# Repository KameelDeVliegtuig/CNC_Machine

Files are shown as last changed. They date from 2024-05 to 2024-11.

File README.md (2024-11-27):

# CNC machine met ingebouwde beveiliging

- 3-assige CNC machine
- Foutherkenning
- Rpi 4B 8GB

## Documentation

Pi's standard network is Houtenbos.

### Steppermotors, Spindle, Buttons & Switches

#### Stepper Steps per mm

| Axis | Steps | mm |
| ---- | ----- | -- |
| X | 80 | 1 |
| Y | 80 | 1 |
| Z | 400 | 1 |

#### Directions

| Direction| X | Y | Direction | Z | Direction | Spindle |
| --- | - | - | --- | - | --- | --- |
| Left | `NULL` | `NULL` | Up |  `true` | Clockwise *Right* | `true` |
| Right | `NULL` | `NULL` | Down | `false` | Counter clockwise *Left* | `false` |

> [!CAUTION]
> **Only change direction of motors when idle or at low RPM!**

#### Stepper Spindle-offset

| Axis | Offset (mm) |
| ---- | --- |
| X | 0 |
| Y | 20 |
| Z | 21.5 |

#### Contact type buttons & switches

| Switch/Button | Contact type | Usage |
| --- | --- | ----- |
| Limit switch X | NC / active `LOW` | Used for zero-ing spindle's X-axis |
| Limit switch Y | NC / active `LOW`| Used for zero-ing spindle's Y-axis |
| Limit switch Z | NO / active `HIGH`| Used for zero-ing spindle's Z-axis, is connected via magnets |
| E-Stop | NO | Used to stop all moving parts |
| Emergency button| NC | Takes all power off machine |

>[!NOTE]
> NC (Normally Closed) NO (Normally Open)

### Raspberry commands

| Command | Description |
| --- | --- |
| `./update` | To speed up the test process a command is used to combine ``` git pull ``` , ``` dotnet build ``` and ``` dotnet ../-.ddl ``` |
| `./stop` | The emergensy stop is used to immedialty disable spindle and steppers |
| `./run`| Runs the .ddl file without compiling |

> [!CAUTION]
> **Usage of `./stop` may brick PWM signal until reboot!**

### [PresenceDetector class](Code/CNC_Interpreter_V2/PresenceDetector.cs)

### [GPIOControl class](Code/CNC_Interpreter_V2/GPIOControl.cs)

```C#
public class GPIOControl
```

In order to use the Gpio pins on the Raspberry pi and MCP23017 multiple functions are used

#### Control functions

##### ControlSpindel

```C#
public boolean ControlSpindel(int speed, bool Dir);
```

This function is used to control the spindle speed and direction.

> [!IMPORTANT]
> Int speed is used as a precentage of the actual speed.

When speed is equal to 0 the spindle will perform a softstop to minimize load to the motor and controller.
When speed is less than 0 (-1), the spindle will perform an emergency stop. With this stop the spindle will stop immediatly. This has a negetive effect on the spindle.
returns true if completed

##### ControlStep

```C#
public bool ControlStep(bool dir, enum GPIOControl.StepperAxis);
```

This function controls the steppers. Usage pretty clear.
returns true if completed

##### Code defined emergency stop

```C#
public bool EmergencyStop(void);
```

Stops all active components

#### Read Functions

##### ReadPin

> [!NOTE]
> Only used for non declared pins

```C#
public bool ReadPin(int Pin, bool IsOnExtender);
```

Returns state of pin.

> [!WARNING]
> Some pins have the same number on the extender as well as the pi

##### ReadLimitSwitch

```C#
public bool ReadLimitSwitch(enum GPIOControl.LimitSwitch)
```

Returns value when limit switch is pressed.

## Hardware

### Incomplete parts list

- Raspberry Pi Zero 2 W voor CNC besturing
- Stepper motor drivers (A4988)
- Custom PCB
  - MCP23017
  - Shitload JST Connectors
- Stukke Ender 3 V2
- 4 NEMA17
- HLK2450 Human Presence radar

## Useful links

[Default steps ender 3V2](https://www.reddit.com/r/ender3/comments/glbx8b/what_are_the_default_steps_per_mm_on_the_ender_3/)

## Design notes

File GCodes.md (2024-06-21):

# G and M Codes

| Code | Description | Status |
|---|---|---|
| **G Codes** | | |
| G0 / G1 | Linear Move | $${\color{green}STATE}$$ |
| G2 / G3 | Arc or Circle Move | $${\color{green}STATE}$$|
| G4 | Dwell | $${\color{green}STATE}$$|
| G5 | Bézier cubic spline | $${\color{green}STATE}$$|
| G17 | CNC Workspace Plane XY | $${\color{green}STATE}$$|
| G18 | CNC Workspace Plane ZX | $${\color{green}STATE}$$|
| G19 | CNC Workspace Plane YZ | $${\color{green}STATE}$$|
| G21 | Units mm | $${\color{green}STATE}$$ |
| G27 | Park Toolhead | $${\color{green}STATE}$$|
| G28 | Auto Home | $${\color{green}STATE}$$ |
| G42 | Move to mesh coordinate | $${\color{red}STATE}$$ |
| G53 | Move in Machine coordinates (fast move) | $${\color{orange}STATE}$$|
| G54 | Workspace Coordinate System Slot 1 | $${\color{red}STATE}$$ |
| G55 | Workspace Coordinate System Slot 2 | $${\color{red}STATE}$$ |
| G56 | Workspace Coordinate System Slot 3 | $${\color{red}STATE}$$ |
| G57 | Workspace Coordinate System Slot 4 | $${\color{red}STATE}$$ |
| G58 | Workspace Coordinate System Slot 5 | $${\color{red}STATE}$$ |
| G59 | Workspace Coordinate System Slot 6 | $${\color{red}STATE}$$ |
| G59.1 | Workspace Coordinate System Slot 7 | $${\color{red}STATE}$$ |
| G59.2 | Workspace Coordinate System Slot 8 | $${\color{red}STATE}$$ |
| G59.3 | Workspace Coordinate System Slot 9 | $${\color{red}STATE}$$ |
| G60 | Save Current position | $${\color{red}STATE}$$ |
| G61 | Return to saved position | $${\color{red}STATE}$$ |
| G91 | Relative Positioning (default) |$${\color{green}STATE}$$|
| G92 | Set Position (Disable <0 values) |$${\color{orange}STATE}$$|
| **M Codes** |
| M0 / M1 | Unconditional STOP |$${\color{green}STATE}$$|
| M3 | Turn on Spindle CW | $${\color{green}STATE}$$|
| M4 | Turn on Spindle CCW | $${\color{green}STATE}$$|
| M5 | Turn off Spindle | $${\color{green}STATE}$$|
| M16 | Device checker | $${\color{green}STATE}$$|
| M18 / M84 | Disable all steppers |$${\color{green}STATE}$$|
| M20 | List Items | $${\color{green}STATE}$$ |
| M23 | Select file | $${\color{green}STATE}$$ |
| M24 | Start/Resume | $${\color{red}STATE}$$ |
| M25 | Pause | $${\color{red}STATE}$$ |
| M27 | Report Execution Status | $${\color{green}STATE}$$ |
| M28 / M29 | Start/Stop Write to SD Card | $${\color{red}STATE}$$ |
| M30 | Delete file from SD | $${\color{red}STATE}$$ |
| M31 | Print Time |$${\color{green}STATE}$$|
| M32 | Begin from SD File | $${\color{red}STATE}$$ |
| M42 | Set pin state (Digital pins on extender) |$${\color{orange}STATE}$$|
| M73 | Manually set progress (LCD) | $${\color{green}STATE}$$ |
| M75 | Start Print Job Timer (LCD) | $${\color{red}STATE}$$ |
| M76 | Pause Print Job Timer (LCD) | $${\color{red}STATE}$$ |
| M77 | Stop Print Job Timer (LCD) | $${\color{red}STATE}$$ |
| M100 | Free Memory | $${\color{green}STATE}$$|
| M105 | Temperature Report |$${\color{green}STATE}$$|
| M112 | Full Shutdown | $${\color{green}STATE}$$|
| M114 | Get Current Position |$${\color{green}STATE}$$|
| M115 | Firmware Info |$${\color{green}STATE}$$|
| M117 | Set LCD Message |$${\color{green}STATE}$$|
| M119 | Endstop States | $${\color{green}STATE}$$|
| M149 | Set Temperature Units (C/F/K) (Fixed at C) | $${\color{green}STATE}$$|
| M150 | Set LED(strip) RGB(W) Color | $${\color{red}STATE}$$ |
| M206 | Home Offset | $${\color{red}STATE}$$ |
| M226 | Wait for pin state (0/1/-1) |$${\color{orange}STATE}$$|
| M256 | Set/Get LCD Brightness | $${\color{red}STATE}$$ |
| M300 | Play Tone | $${\color{red}STATE}$$ |
| M305 | Set MicroStepping (Fixed at 1/16) |$${\color{green}STATE}$$|
| M400 | Wait for moves to finish |$${\color{green}STATE}$$|
| M401 | Deploy Bed Probe |$${\color{green}STATE}$$|
| M402 | Stow Bed Probe |$${\color{green}STATE}$$|
| M410 | Stop all stepper instantly |$${\color{green}STATE}$$|
| M420 | Get/Set Bed Leveling State | $${\color{red}STATE}$$ |
| M428 | Set Home at Current Position |$${\color{green}STATE}$$|
| M510 | Lock Machine |$${\color{green}STATE}$$|
| M511 | Unlock Machine |$${\color{green}STATE}$$|
| M512 | Set Passcode |$${\color{green}STATE}$$|
| M524 | Abort Print in Progress | $${\color{red}STATE}$$ |
| M575 | Change Serial BaudRate | $${\color{red}STATE}$$ |
| M928 | Start Logging to SD | $${\color{red}STATE}$$ |
| M995 | Calibrate Touchscreen | $${\color{red}STATE}$$ |
| **Custom Codes** |
| X0 | Selective Stop |$${\color{orange}STATE}$$|

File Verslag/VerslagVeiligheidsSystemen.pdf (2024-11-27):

## Implementatie van Veiligheidstechnologieen in een Aangepaste CNC-freesmachine ¨

Lasse Houtenbos
InHolland University of Applied Sciences Alkmaar, Netherlands
Email: 697293@student.inholland.nl

Abstract—Dit document beschrijft de veiligheidsmaatregelen voor een zelf gebouwde CNC-freesmachine uit een Ender 3 V2 [1]. Om ongelukken met mensen te voorkomen is de machine uitgerust met een Human Presence radar om de aanwezigheid van mensen in de buurt van te detecteren en zo de veilige werking te verzekeren. Deze introductie biedt een overzicht van de gebruikte technologie.

### 1. Introductie

Veiligheid is een belangrijk onderdeel bij het gebruik van een CNC-freesmachine, door de draaiende en scherpe onderdelen is het een gevaarlijke machine. Veel machines hebben om deze reden ook meerdere veiligheids maatregelen ingebouwd. Verschillende soorten beveiliging kunnen worden gebruikt om ongelukken te voorkomen. Zo de machine zo veilig mogelijk te maken worden in veel machines meerdere veiligheids maatregelen genomen. In dit artikel worden alleen de veiligheidsmaatregelen besproken die de veiligheid van mensen kunnen waarborgen

### 2. Onderzoeksvragen

In dit onderzoek richten we ons op de verbetering van veiligheidsmaatregelen voor CNC-freesmachines. De volgende onderzoeksvragen zijn geformuleerd om de richting van dit onderzoek te bepalen:

1) Welke risico’s vormen de grootste bedreiging voor de veiligheid van operators bij het gebruik van CNC-freesmachines?
2) Hoe effectief zijn bestaande fysieke en softwarematige beveiligingsmechanismen in het voorkomen van ongevallen bij CNC-freesmachines?
3) Kan de integratie van Human Presence Radartechnologie de veiligheid van CNC-freesmachines significant verbeteren en hoe?

### 3. Bestaande oplossingen

### 3.1. Noodstopknoppen

Noodstopknoppen zijn fysieke knoppen die rondom de machine zijn geplaatst. Deze knoppen kunnen handmatig worden ingedrukt om de machine onmiddellijk te stoppen in geval van een noodsituatie. Dit biedt een snelle manier om de machine uit te schakelen en verdere schade te voorkomen. Binnen de noodstoppen zijn er verschillende varianten. Zoals de E-Stop, deze stop zal alle bewegende delen van de machine softwarematig uitschakelen. Een andere variant is de hard-stop, deze knop sluit de machine af van alle spanning. Het probleem met een hard-stop is dat de machine in uitgeschakelde toestand alle bewegende delen alsnog zo abrupt mogelijk stil moet zetten.

### 3.2. Fysieke Afschermingen

Fysieke afschermingen, zoals veiligheidsdeuren en omheiningen, beperken de toegang tot gevaarlijke delen van de machine tijdens de werking. Deze afschermingen zorgen ervoor dat operators en omstanders niet per ongeluk in contact komen met bewegende delen of snijgereedschappen. Vaak zijn deze afschermingen digitaal gekoppeld aan de machine, door deze extra vorm van beveiliging weigert de machine te werken bij kapotte of falende afschermingen. In het geval van deze CNC-freesmachine zijn fysieke afschermingen niet mogelijk door het gebruik van een bestaande 3D printer.

### 3.3. Softwarematige Veiligheidscontroles, Sensoren

Softwarematige veiligheidscontroles omvatten verschillende functies binnen de besturingssoftware van de machine. Dit kan het controleren van bewegingslimieten, snelheden en andere onderdelen omvatten om te voorkomen dat de machine in een gevaarlijke toestand opereert. Foutdetectie en automatische uitschakeling bij abnormale omstandigheden zijn ook onderdeel van deze beveiligings.

### 3.4. Human Presence Radar (HPR)

De Human Presence radar is een sensor die elektromagnetische golven gebruikt om de aanwezigheid en locatie van mensen te detecteren [2]. Deze sensor is hierdoor uitermate geschikt als beveiligingsmaatregelen. Een voordeel aan een HPR is dat de afstand en locatie van de omstander of operator ook meetbaar is. Met deze functie kan geanticipeerd worden op bewegingen van mensen.

Wanneer menselijke aanwezigheid wordt gedetecteerd, kan de machine automatisch worden uitgeschakeld of in een veilige modus worden gezet. Dit biedt uitkomst in grote machines waar fysieke afschermingen of hekken de werking en onderhoud van de machine belemmeren.

### 4. Methode

### 4.1. Hardware

### 4.1.1. Printplaten. Om alle onderdelen goed en op een

nette manier met elkaar te verbinden wordt gebruik gemaakt van een custom designed PCB. Een voordeel van een PCB is dat de juiste spanningen ook op het bord worden gegenereerd. Op deze PCB zitten meerdere aansluitingen voor alle onderdelen. Op deze printplaat zitten ook de aansluitingen voor de sensoren en knoppen voor het beveiligingsmechanisme. De controllers voor de motoren worden ook op deze printplaat bevestigt.

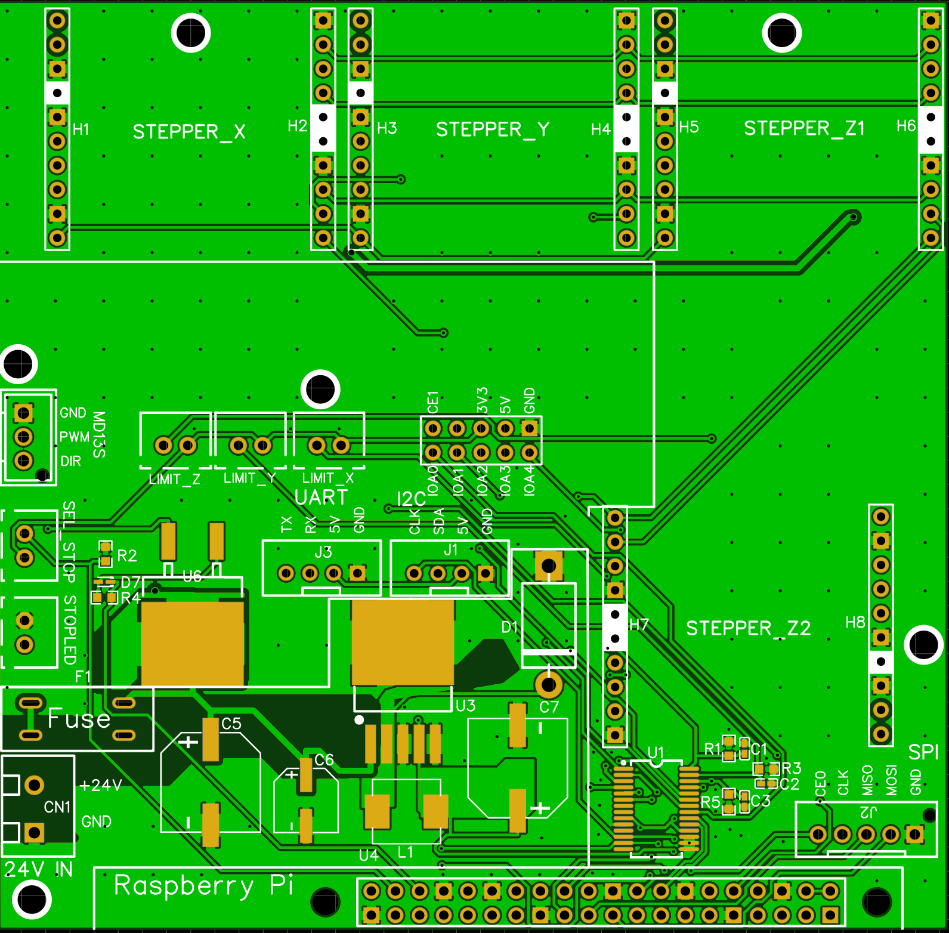
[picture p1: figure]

Figure 1. Main PCB

### 4.1.2. Main Controller. Als brein van de CNC machine

is een Raspberry Pi Zero W 2 [3], deze chip beschikt over een sneller processor en meerdere cores. De keuze is uitgegaan naar deze chip door zijn kleine vorm maar alsnog goede performance. Ook heeft de Pi Zero meerdere verbindingsmogelijkheden, zowel draadloos als bedraad. Hierdoor is de Pi Zero perfect voor onze machine

### 4.1.3. HPR. De gebruikte HPR is de LD2450 van HiLink

[4]. Deze sensor is gekozen door de detectie snelheid en prijs van de sensor maar ook door de opties van de sensor op het communicatie vlak.

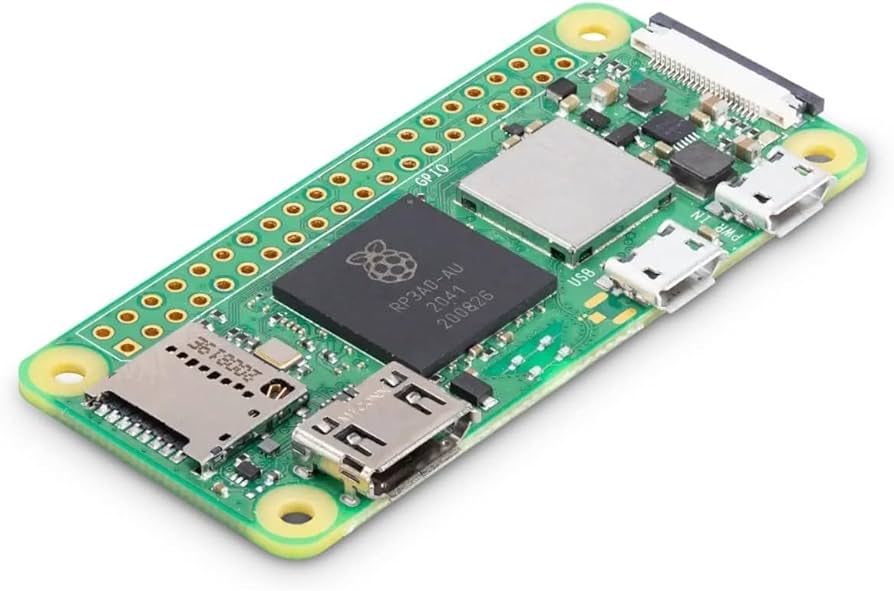
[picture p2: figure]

Figure 2. Raspberry Pi Zero W 2

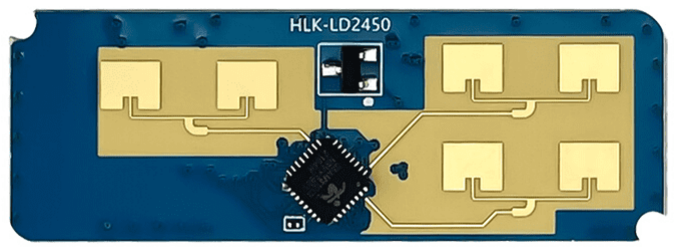
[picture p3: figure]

Figure 3. Hilink LD2450

### 4.2. Noodstop

De CNC machine is ook uitgerust met een E-Stop en een Noodstop. Deze twee knoppen zijn verwerkt in een kleine behuizing die bevestigt is aan een lange kabel. De E-Stop heeft een verbinding met de Raspberry pi, en kan de motoren en bewegingen van de machine snel uitschakelen. Het grote verschil tussen de E-Stop en de Noodstop is eerder benoemd, daarom schakelt de Noodstop de spanning van de machine af.
Het verschil in gebruik is erg belangrijk. Bij gebruik van de E-stop zal de machine nagenoeg gelijk stil staan, maar bij gebruik van de noodstop heeft de machine tijd nodig om compleet stil te staan.

### 4.2.1. Spindel driver. Een CNC-machine maakt gebruik

van een frees om zo delen van het materiaal weg te halen. Om deze functie uit te voeren heeft de frees een hoog aantal toeren nodig. Hiervoor wordt een DC-motor gebruikt deze is snel op toeren, hoog toerental en vooral krachtig, maar deze motor vereist veel stroom om te goed te functioneren. Dit geeft een belemmering voor de besturing van de motor. Om dit te versimpelen is er gebruk gemaakt van een H-Brug [4]. Deze H-Brug is los van de primaire PCB en maar wordt aangestuurd via de primaire PCB. Dit is op deze manier gedaan om zo min mogelijk stroom door de primaire PCB te laten lopen. Deze H-Brug kan de directie en de snelheid van de motor bepalen. Met deze H-Brug kan de motor dus tot een gecontroleerde stop gebracht worden zonder grote piekstromen of andere problemen te veroorzaken. In noodsituaties is de gecontroleerde stop te langzaam, daarvoor is de noodstop. Met deze stop veranderd de H-Brug voor een hele korte periode de directie van de motor, waarna deze in een klap stilstaat. Dit is erg negatief voor de levensduur van de motor. Daarom wordt deze rem alleen gebruikt in noodsituaties. [MD13s] [5]

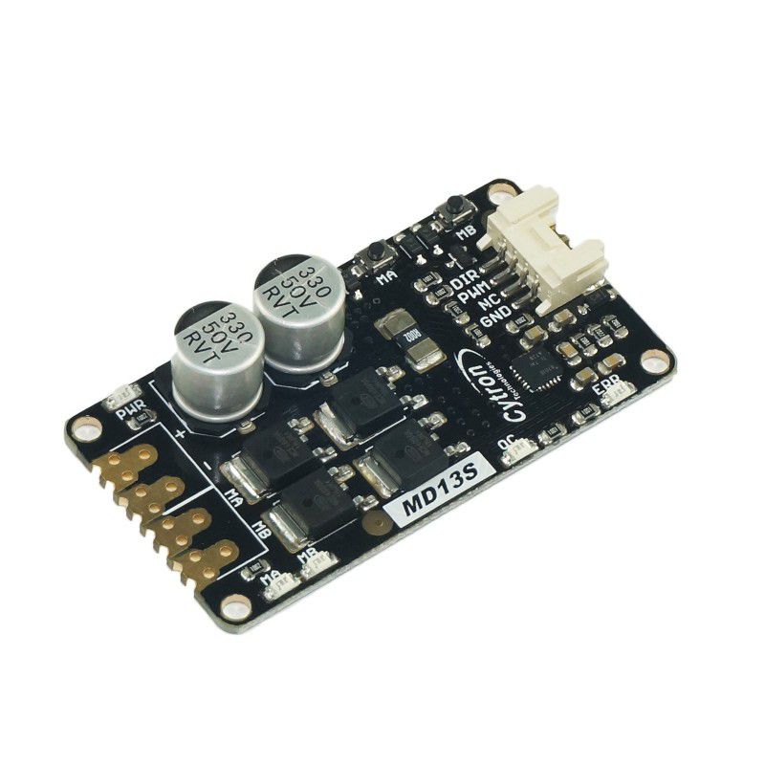
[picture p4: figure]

Figure 4. Cytron MD13S

### 4.3. Software

### 4.3.1. Sensor. De LD2450 communiceert met de Raspberry

pi, de HPR geeft alleen de afstand van de dichtsbijzijnde persoon door aan de Pi. Dit om onnodige data van de lijn af te houden. Hierna berekent de pi de locatie van de persoon. Met deze data bepaald de Pi of de machine lager in toeren moet gaan draaien om zo de stop sneller en soepeler te laten verlopen, of de machine te stoppen. Deze virtuele ”hekken” kunnen ingesteld worden via meerdere variabelen in de code om zo een soepele werking van de machine te garanderen. De LD2450 kan op verschillende manieren communiceren, via Bluetooth en UART[4.3.1]. In deze machine is UART gebruikt, dit omdat de LD2450 de veiligheid van de machine waarborgt en dit niet veilig is via een soms instabiele draadloze verbinding. [6], [7]

UART. Het Universal Asynchronous Receiver/Transmitter (UART) protocol [8] is een serieel communicatiepro- ¨ tocol dat wordt gebruikt voor het verzenden en ontvangen van data tussen apparaten. UART wordt vaak toegepast in embedded systemen, microcontrollers, en communicatie tussen randapparatuur en computers.
UART werkt op basis van twee signaallijnen:
- Tx (Transmit): Deze lijn wordt gebruikt om gegevens van de verzendende naar de ontvangende kant te sturen. De verzendende kant converteert parallelle gegevens naar seriele vorm en stuurt deze via ¨ Tx.
- Rx (Receive): Deze lijn wordt gebruikt om gegevens van de ontvangende naar de verzendende kant te ontvangen. De ontvangende kant converteert de ontvangen seriele gegevens terug naar parallelle gegevens. ¨

UART maakt gebruik van een baudrate om de snelheid van gegevensoverdracht te specificeren, zoals 9600 bps (bits per seconde) of 115200 bps. De communicatie is asynchroon, wat betekent dat er geen apart kloksignaal wordt gebruikt om de timing van de gegevensoverdracht te synchroniseren. In plaats daarvan worden start- en stopbits toegevoegd aan elk gegevensframe om de grenzen van de overdracht aan te geven.
De werking van UART omvat het verzenden van gegevensframes die bestaan uit een startbit (laag niveau), gevolgd door de data bits (meestal 7 of 8 bits), en tot slot een of meer stopbits (hoog niveau) om het einde van het frame aan te geven. Dit eenvoudige maar duidelijke protocol maakt UART geschikt voor betrouwbare seriele communicatie. ¨ De LD2450 heeft een specifieke manier om data te versturen. Deze wordt ontcijferd door de software.
1 | private void ProcessBuffer()
2 | {
3 | int i = 0;
4 | while (i <= bufferIndex - DataLength)
5 | {
6 | // Check for the header and end of frame
| bytes
7 | if (buffer[i] == 0xAA && buffer[i + 1] ==
| 0xFF && buffer[i + 2] == 0x03 && buffer[i + 3]
| == 0x00 &&
8 | buffer[i + DataLength - 2] == 0x55 &&
| buffer[i + DataLength - 1] == 0xCC)
9 | {
10 | // Extract the valid frame
11 | byte[] frame = new byte[DataLength];
12 | Array.Copy(buffer, i, frame, 0,
| DataLength);

13
14 | // Process the frame
15 | ProcessFrame(frame);

16
17 | // Move past this frame in the buffer
18 | i += DataLength;
19 | }
20 | else
21 | {
22 | i++;
23 | }
24 | }
25 | }
4.3.2. Noodstoppen.
E-stop. De E-stop beschikt over een ingebouwde LED die de status van de machine kan laten zien. Wanneer de knop ingedrukt wordt pauzeert de machine de code die op dat moment uitgevoerd word, hierna worden alle bewegende delen afgeschakeld en geremd. De freesmotor remt hier met de noodstop waardoor deze in e´en keer ´ stil staat. De E-stop wordt ook digitaal ingedrukt bij het overschrijden van het virtuele hek van de machine.

Noodstop. De noodstop is een grote rode knop die ingedrukt wordt in geval van een mechanische of softwarematige fout. Denk hierbij aan gecrashte code waardoor de freeskop op volle toeren draait, of brand in de machine. Met deze knop wordt de complete machine afgeschakeld van de spanning en stoppen alle delen met werken.

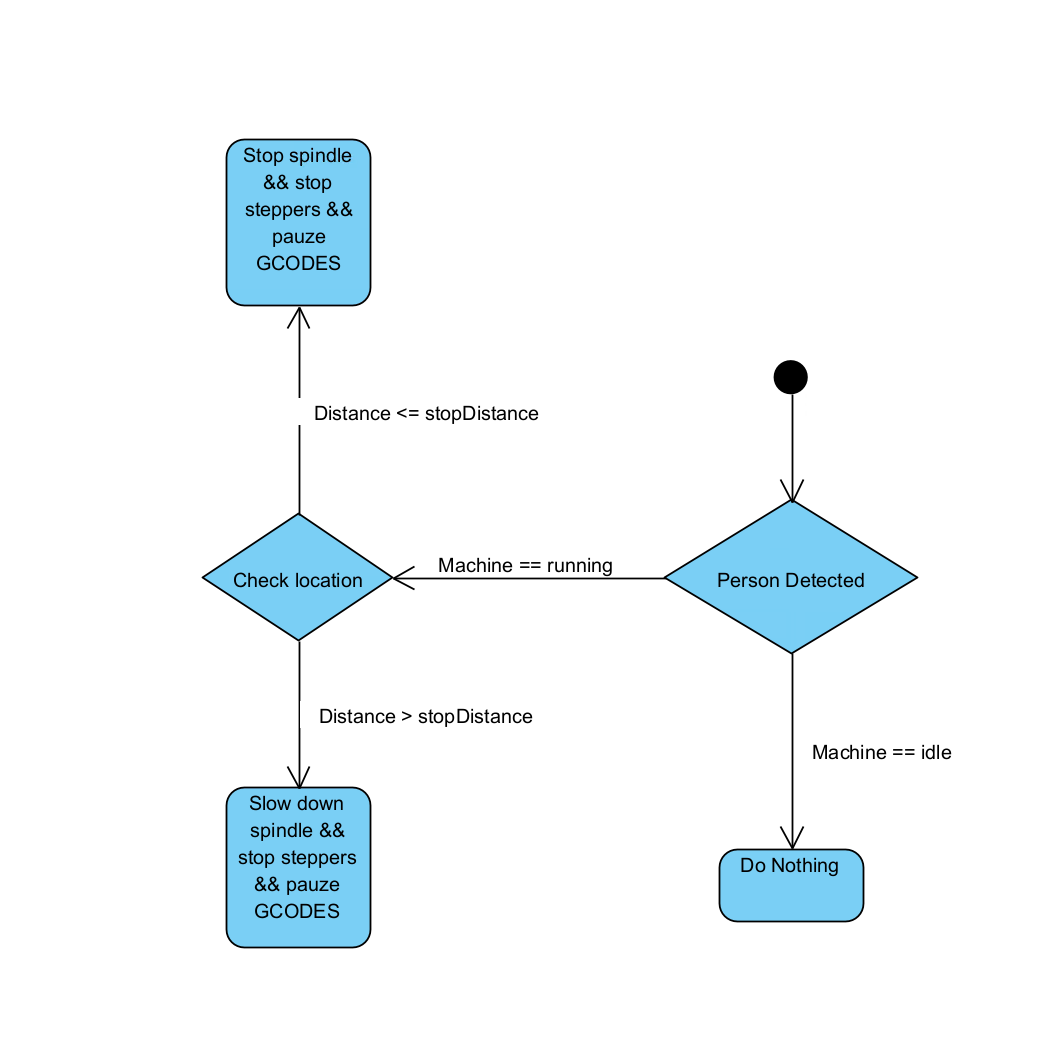
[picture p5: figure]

Figure 5. Klasse diagram

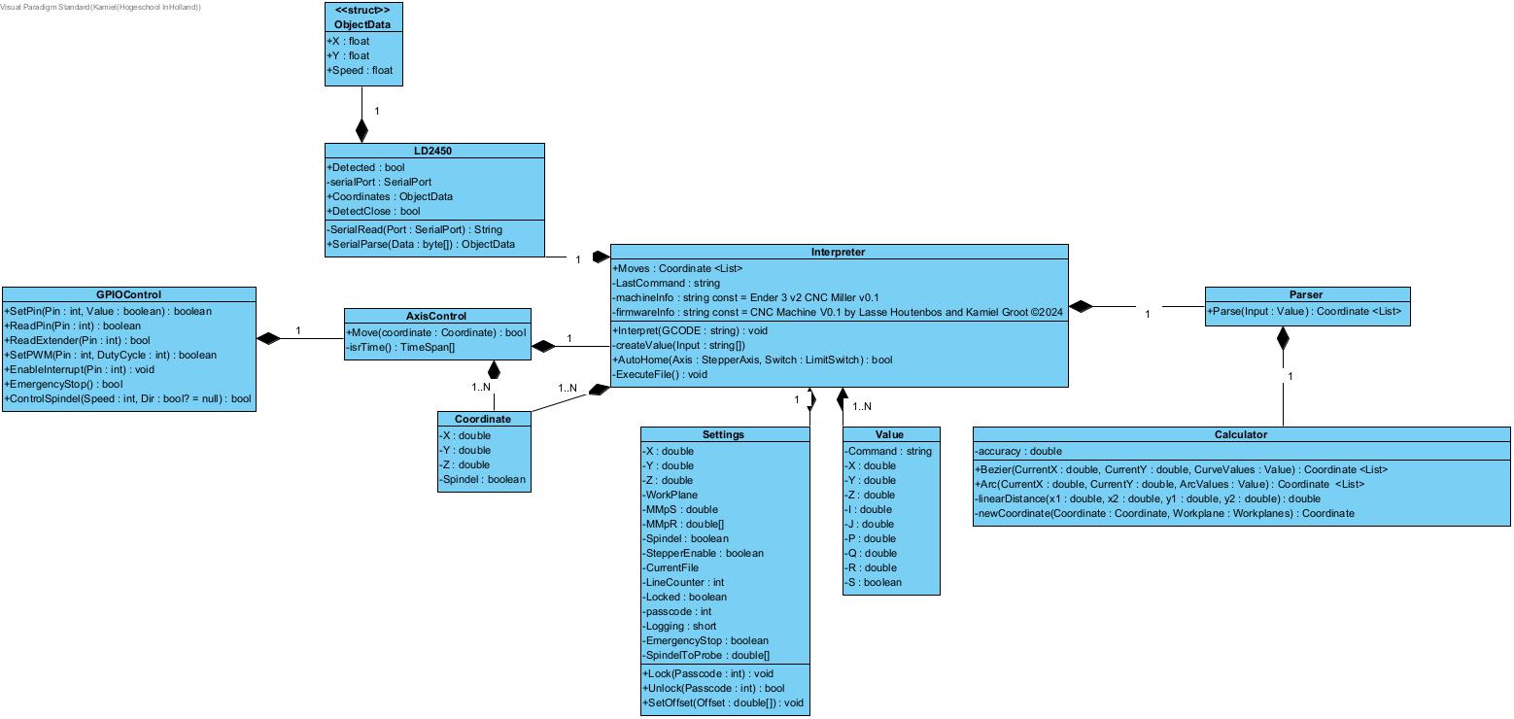
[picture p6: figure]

Figure 6. UML Diagram

4.3.3. Diagrammen.

### 5. Conclusie

Dit document heeft de veiligheidsmaatregelen besproken die zijn ge¨ımplementeerd in een zelfgebouwde CNC-freesmachine, met een focus op het waarborgen van de veiligheid van gebruikers. De machine maakt gebruik van verschillende technologische oplossingen, waaronder noodstopknoppen, softwarematige veiligheidscontroles en een Human Presence Radar (HPR).

De noodstopknoppen, inclusief de E-Stop en Noodstop, bieden een snelle manier om de machine in noodsituaties te stoppen. Echter, het is belangrijk op te merken dat de huidige implementatie van de noodstop niet altijd de ideale reactie biedt. De noodstop zou de machine volledig en direct moeten uitschakelen zonder nadelige gevolgen voor de apparatuur, wat momenteel niet volledig wordt bereikt. De HPR, zoals de LD2450 van HiLink, toont veelbelovende resultaten in het detecteren van menselijke aanwezigheid rond de machine. Deze radar biedt niet alleen de mogelijkheid om de machine automatisch uit te schakelen bij detectie van personen, maar kan ook de machineaanpassingen stroomlijnen om soepelere en veiligere operaties te waarborgen. De kosten-effectiviteit van de LD2450 maakt het een aantrekkelijke keuze voor integratie in machines zoals deze CNC-freesmachine. De enigelimitatie van deze sensor is de reactie snelheid en precisie van de sensor. In het getoonde prototype zijn deze limitaties geen probleem, maar in een uiteindelijke CNC-machine is deze sensor uiterst ongeschikt.

### 6. Aanbeveling

Om de veiligheid te verbeteren, is het cruciaal om de werking van de noodstop te verbeteren, zodat deze betrouwbaar en consistent reageert in noodsituaties zonder dat dit negatieve gevolgen heeft voor de apparatuur. Dit vereist mogelijk aanpassingen aan de elektrische schakelingen en software-algoritmen die verantwoordelijk zijn voor de noodstopfunctionaliteit.
Verder onderzoek naar geavanceerde sensorsystemen en automatiseringstechnologieen, zoals machine learning- ¨ algoritmen voor bewegingsdetectie en real-time besluitvorming, zou kunnen bijdragen aan nog veiligere en efficientere ¨ CNC-machines.

### References

[1] Creality, “Ender-3 v2,” 2023. Accessed 20-05-2024, https://www.creality.com/products/ender-3-v2-3d-printer-csco.
[2] Y. Benezeth, H. Laurent, B. Emile, and C. Rosenberger, “Towards a sensor for detecting human presence and characterizing activity,” Energy and Buildings, vol. 43, no. 2-3, pp. 305–314, 2011.
[3] Raspberry Pi Co., “Raspberry pi zero 2 w,” 2021. Accessed 06-06-2024, https://www.raspberrypi.com/products/raspberry-pi-zero-2-w/.
[4] Hi-Link Electronic Co., Ltd., “24ghz human presence detection module,” 2024. Accessed: 2024-06-17.
[5] Cytron Technologies, “13amp 6v-30v dc motor driver,” 2016. Accessed: 2024-06-17.
[6] “Github cnc machine code.” https://github.com/KameelDeVliegtuig/ CNC Machine. (https://github.com/KameelDeVliegtuig/CNC_Machine)
[7] L. | Shenzhen | Hi-Link | Electronic | Co., | HLK-LD2450Motion
target | detection | and | tracking | module | Instruction
manual, | 2023. | https://drive.google.com/drive/folders/
1kTt0Z3hjKKrIF3OCIDGdwQ4KotDJ8SGA. (https://drive.google.com/drive/folders/1kTt0Z3hjKKrIF3OCIDGdwQ4KotDJ8SGA)
[8] E. Pena and M. G. Legaspi, “Uart: A hardware communication pro- ˜ tocol understanding universal asynchronous receiver/transmitter,” Visit Analog, vol. 54, no. 4, pp. 1–5, 2020.

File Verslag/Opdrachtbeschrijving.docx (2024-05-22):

# CNC Vreesmachine

Het doel is om een CNC vreesmachine te ontwikkelen waarvan de firmware volledig in C# is geschreven. Een CNC (Computer Numerical Control) vreesmachine is een computergestuurde machine die materialen zoals hout, metaal of kunststof kan weghalen door middel van een draaiende vrees.
De machine gebruikt een Human Presence Radar (HPR) om de veiligheid te waarborgen door de machine automatisch stil te zetten als iemand te dicht in de buurt komt.

De machine gebruikt in eerste instantie een commandline interface. Bij meer tijd zal hier een mooie Graphical User Interface (GUI) voor gemaakt worden.

## Firmware Ontwikkeling

Basisfunctionaliteit van de CNC machine moeten geprogrammeerd worden, dit omvat de ontwikkeling van de kernfunctionaliteiten van de machine, zoals het aansturen van de freeskop en het beheren van de verschillende machineprocessen.
Deze machineprocessen zijn onder andere:

- De bewegingsbesturing (X, Y, Z assen): Het programmeren van de bewegingen van de freeskop langs de X, Y en Z assen.
- Vreeskopaansturing: Het instellen van de snelheid van de vreeskop.
- Veiligheidsmechanismen: Het integreren van veiligheidsmechanismen, waaronder de later beschreven HPR en een noodstop functie, om de machine onmiddellijk te kunnen stilzetten bij gevaarlijke situaties.

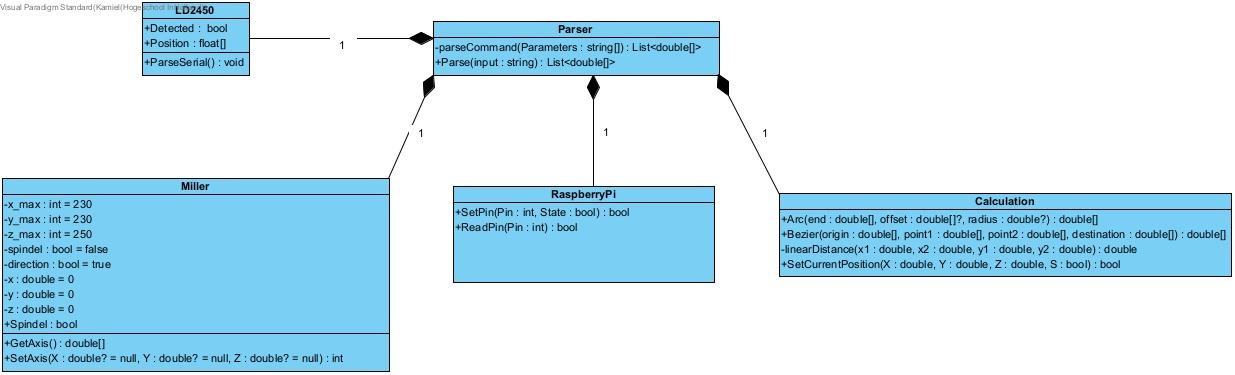
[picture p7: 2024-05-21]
OO/GCodeParsing.jpg

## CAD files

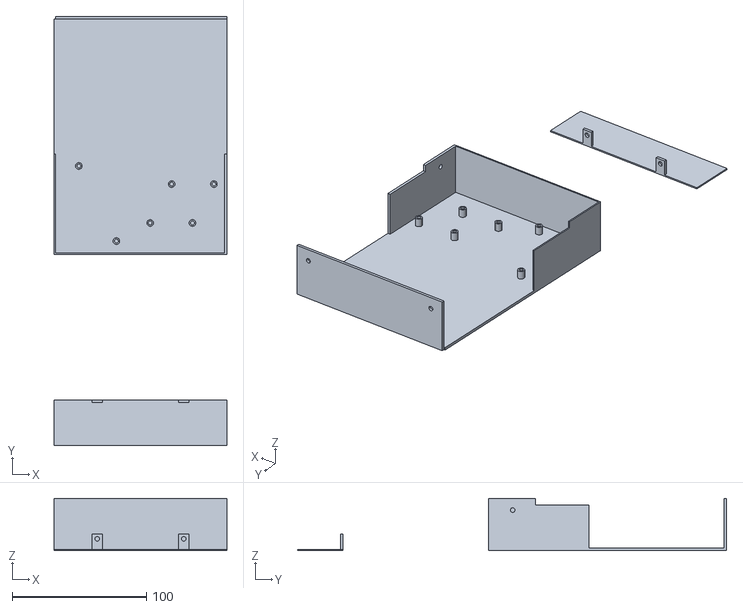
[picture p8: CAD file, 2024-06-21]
3D Files/BakjeCNCPCBShizzle v1.stl
129.0 x 320.0 x 39.0

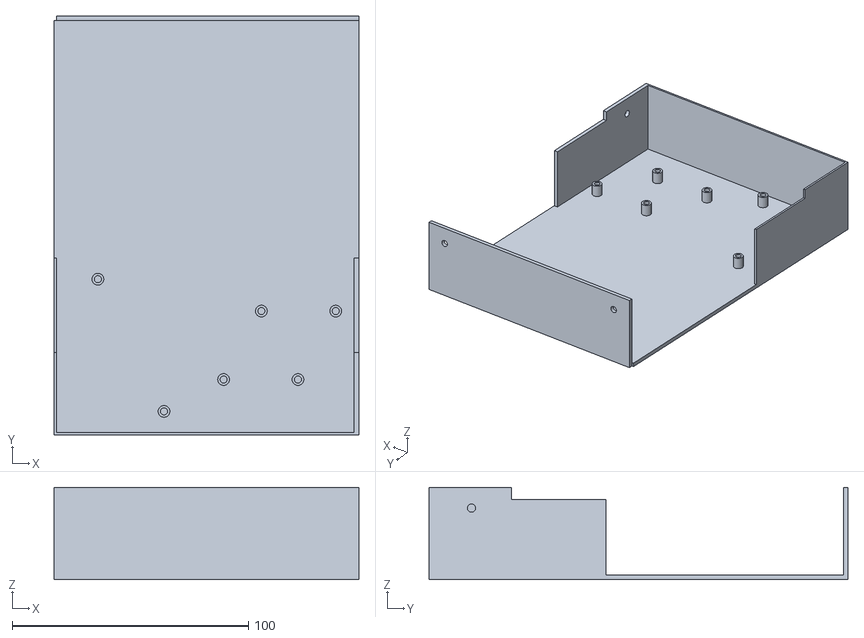
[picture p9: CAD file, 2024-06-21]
3D Files/Box.stl
129.0 x 177.5 x 39.0

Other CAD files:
3D Files/BakjeCNCPCBShizzle v1.f3d
3D Files/BracketLD2450.f3d
3D Files/MotorMountBracket.f3d
3D Files/Z_LimitSwitchBox.f3d

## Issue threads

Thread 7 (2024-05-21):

UART won't receive on Pi

Lassehoutenbos, 2024-05-21:
Possible TX RX mixup

Closed 2024-06-18.

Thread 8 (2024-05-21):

HPR debuggen

Lassehoutenbos, 2024-05-21:
**issue #7  needs to be fixed first**

Debug UART data and enhance code

Closed 2024-06-18.

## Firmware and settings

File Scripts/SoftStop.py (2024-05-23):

#!/usr/bin/env python2.7
# https://raspi.tv/2013/how-to-use-interrupts-with-python-on-the-raspberry-pi-and-rpi-gpio
import RPi.GPIO as GPIO
import os as os
import time as time
GPIO.setmode(GPIO.BCM)
# GPIO 23 set up as input. It is pulled up to stop false signals
GPIO.setup(20, GPIO.IN)
# now the program will do nothing until the signal on port 23
while (GPIO.input(20) == GPIO.LOW) :
   time.sleep(.01)

print ("Stopping the system")
os.chdir('/home/cnc')
os.system('./stop')       # clean up GPIO on CTRL+C exit
GPIO.cleanup()
"""
The above code is a python script that will be run on the Raspberry Pi. This script listens for a signal on GPIO pin 20. When a signal is detected, the script will run a bash script that will stop the system. The bash script is as follows:
The stop script will stop the system when run. The system will then need to be manually powered back on in order to restart it.
"""

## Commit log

2024-04-23 Added I2C for MCP23017
2024-05-04 Added 3DFiles
    [BracketLD2450.f3d]
2024-05-04 Added multiple 3D files
    [MotorMountBracket.f3d, Z_LimitSwitchBox.f3d]
2024-05-18 Test van board
2024-05-18 Edit PWM
2024-05-18 PWM Rev
2024-05-19 Test Y axis
2024-05-19 Z axis
2024-05-19 Test limit switches
2024-05-20 Test PWM
2024-05-21 PWM chip gekut
2024-05-21 PWM channel fixed
2024-05-21 PWM test
2024-05-21 Added Console debugging to SpindelControl and PWM Control
2024-05-21 Testing Spindle
2024-05-21 Stepper X asis Test
2024-05-21 Spindle move test
2024-05-21 Stopped Spindle
2024-05-21 Added controlled stop to spindle function Added immediate stop to spindle function
2024-05-21 Cleaned GPIOControl Added EmergencyStop Added comments Removed unnecessary test code for spindle part
2024-05-22 Updated schematic
2024-05-22 Testing new Delay in steppers
2024-05-22 Edited README with steppers
2024-05-22 Testing spindle Controlled stop
2024-05-23 Finished Spindle control
2024-05-23 stepper test
2024-05-23 Fixed axis control negative coordinate handling and added ControlStep to Timer Elapsed functions
2024-05-24 Added Disable steppers Added public SetPin
2024-05-27 Ik hoop dat dit werkt ander spring ik
2024-05-28 Testing UART
2024-05-28 Changed UsDelay to for loop with Thread.Sleep(0) as ControlStepper delay
2024-05-29 Removed Timer.Start exception
2024-05-29 Remade Timers for AxisControl
2024-06-02 Isr Timer test2
2024-06-03 remade Z axis switch logic
2024-06-03 Fixed stepper direction X and Y
2024-06-03 Z axis equal speed
2024-06-04 Made sure M105 temperature is rounded correctly
2024-06-10 Test sensor
2024-06-10 Sensor Testenm
2024-06-11 Added Threading for Detector
2024-06-16 Added additional thread for executing moves
2024-06-21 Changed G-Codes
    [BakjeCNCPCBShizzle v1.f3d, BakjeCNCPCBShizzle v1.stl, Box.stl]
2024-07-02 Removed enable pin stepcontrol
2024-07-02 Turning spindle on after brake
